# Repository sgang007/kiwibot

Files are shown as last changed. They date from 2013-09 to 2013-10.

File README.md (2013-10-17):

<p align="center">
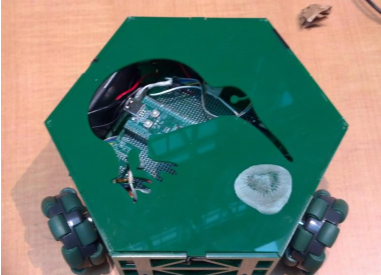
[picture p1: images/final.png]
  
</p>
# Introduction #

An omniwheel robot created for a class project. The robot uses three omniwheels mounted in a equilateral triangle formation to move in any direction without changing its orientation. A line following component was also added to be able to demo its movement easily. The CAD files for the body design, the circuit schematics, and the code are all included. Though only the simpler PID method was tested and used for the final project, I've also included another PID function written afterwards that would need to be tested to tweak the factors before use. 
All the code, cad files, and eagle files are included.

## Body Design ##

The frame was modeled in NX CAD. The part drawings were then saved as DXF files and printed out of .125”-thick, fluorescent green acrylic. The robot assembly was designed to be simple yet sturdy and was accomplished through a combination of press-fits, fastener screws, and hot glue.
The enclosed portion of the frame housed the three 6 volt battery packs, the cylindrical housing for the three motors, as well as the NU32’s PCB. The undercarriage held the motor gearboxes and attached omniwheels as well as the custom PCB with the H-bridges and phototransistor LED ring, described in detail below. The files are attached.

We used the faulhaber motor with encoder described here: http://www.robotroom.com/FaulhaberGearmotor.html 
Our main reason for using these was that they were available in the lab. But we had a few issues with it, such as being able to tighten the set screw. We did not have the right hex key available and so we just used a small screwdriver to tighten it whenever there was an issue. But by the end of the project, this had stripped the screw and made it impossible to tighten the wheels. Luckily we had already demoed by then, but it is the reason for not testing out the new PID.

## Circuit ##

<p align="center">
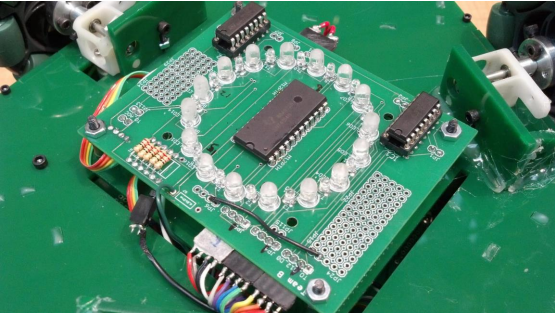
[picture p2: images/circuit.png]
  
</p>

We wanted line sensing, but it wasn't the main objective of the project so this part was kept simple and cheap. Just a ring of LEDs and phototransistors for the line detection. The ring of 16 LED/phototransistor pairs makes the detection cheap and orientation independent. 
We kept most of the circuit elements on the PCB on the underside of the robot where the LEDs would have to be. The phototransistors are connected to a MUX and cycled through by the PIC to read different points on the circle. The circuit was designed in EAGLE and the files are also included.
Images of the schematic are attached. Can't find the Eagle files right now...

## Code ##

The encoder counts are counted by polling the ports at a tiny interval (faster than that of the motor’s fastest rpm * encoder lines) and decoding the quadrature.

The sensing and movement:

(LED 7 was 90 degrees, straight ahead)

1.  If there is no previous forward point saved, set previous forward point to 7

2.  Cycle through LEDs and check “high” phototransistors (those over a dark color)

3.  Collect contiguous blocks of high LEDs (so if LEDs 1-4 were high, that would be one 
block)

4.  Compute the point distance between the previous forward point and the border points of 
each block.

5.  Update previous forward point to the point that is the shortest distance from the previous forward point. (thus 
distinguishing between the front and back of the path)

7.  Convert point to degree heading and pass to movement

The movement algorithm was a simple linear system that was solved for the velocities of each 
wheel. The three parameters were the x,y directions and the angular velocity which we set to 
0 in order to achieve movement without change in orientation. 
We solve for each wheel's velocity by using the amount it would contribute to each direction while keeping rotation zero

## PID ##

The simple PID method we used was to check the speed of the wheel that was supposed to spin the fastest (or pick one 
of the two if two were supposed to spin at equal speeds, like for straight ahead movement) and use it and proportions of it
as the target value to judge error of off for feedback.

Obviously it isn't perfect but it worked for the slower speeds 
with only very slight orientation changes after a while of demoing. But we had a more advanced method we hadn't fully tweaked 
by the time it was due and can't test now due to the broken screw. 

Once again use relative velocities, but make the target an angular velocity of 0.  The error would be amount off 0, and feedback affects all three wheels by k*relative velocity, so wheels are corrected differently 
based on how fast they are going, and wheels rotating the robot in the opposite direction are corrected by the opposite value. 

This looked like it could work better but it was a bit more complicated. And to get it really smooth and going at a decent speed, 
there is the issue of correcting current relative velocities to prevent the orientation change while also keeping target velocities in mind
so that velocities aren't corrected and kept at too low of a speed. And waiting too long after a heading change to correct would mean 
that the orientation would change too much between heading changes. Implementing that and ironing out such issues is the next step.

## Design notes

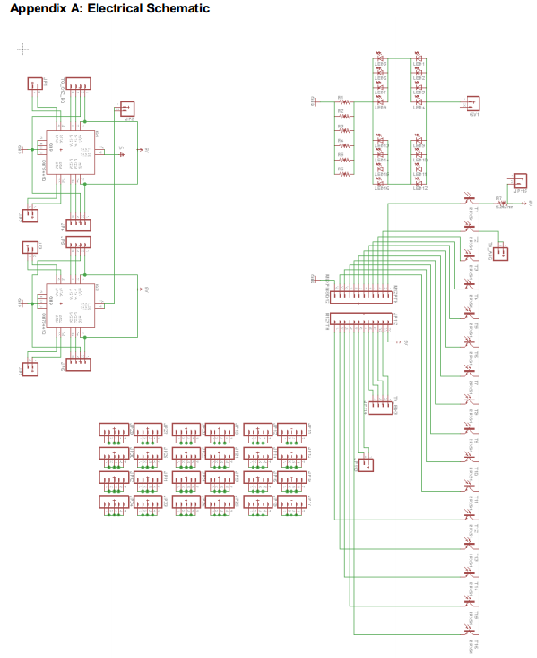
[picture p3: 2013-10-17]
images/circuitschematic.png

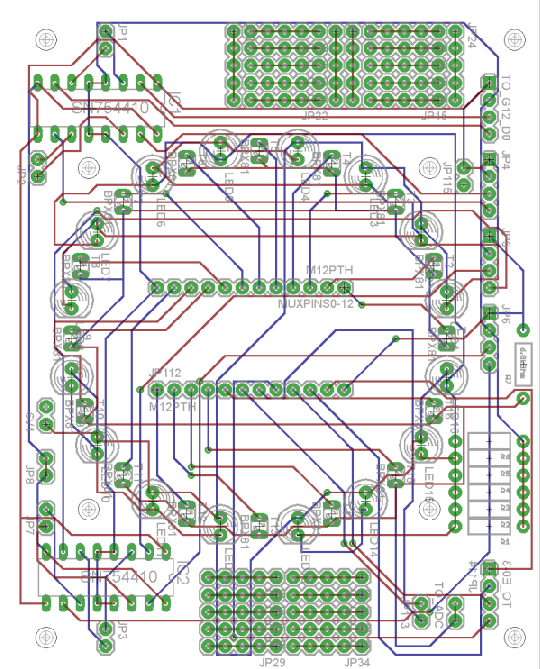
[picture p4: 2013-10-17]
images/pcb.png

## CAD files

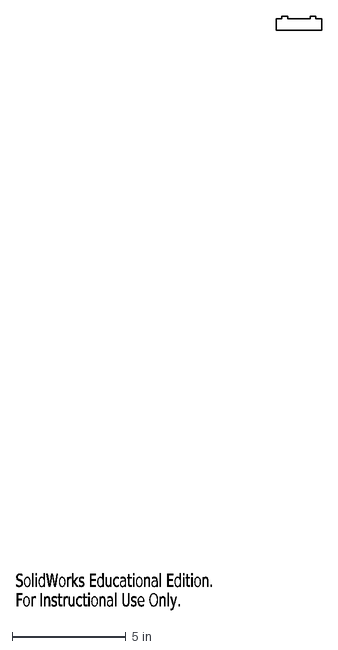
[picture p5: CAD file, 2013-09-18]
DXF/battsupp1.DXF
SolidWorks Educational Edition.
For Instructional Use Only.

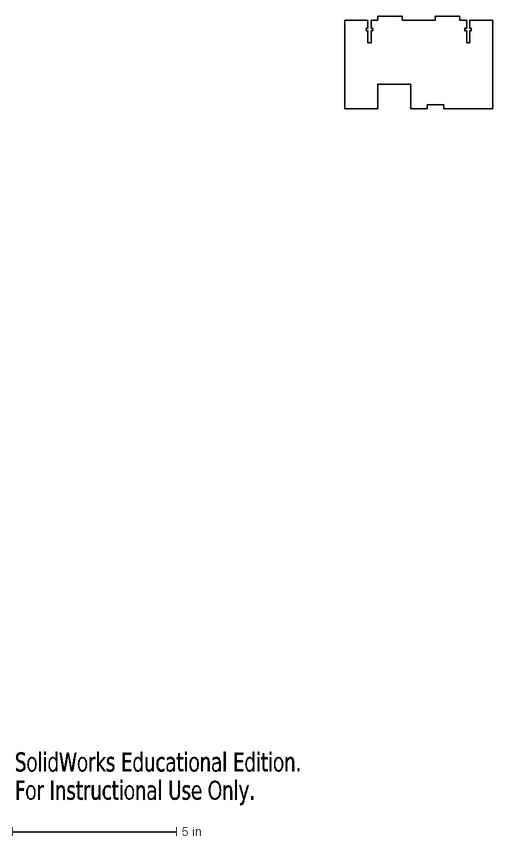
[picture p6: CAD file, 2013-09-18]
DXF/hexside mid.DXF
SolidWorks Educational Edition.
For Instructional Use Only.

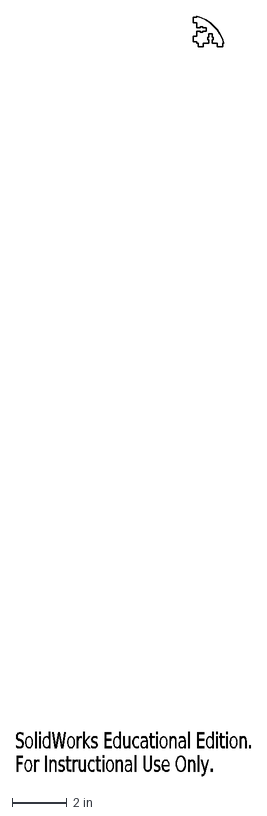
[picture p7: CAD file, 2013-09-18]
DXF/motorsupport2.DXF
SolidWorks Educational Edition.
For Instructional Use Only.

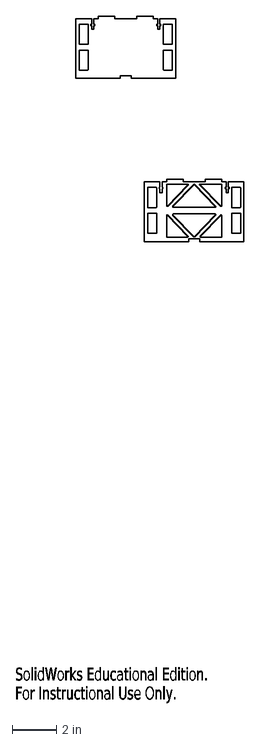
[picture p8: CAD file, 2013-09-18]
DXF/hexside none_0.DXF
SolidWorks Educational Edition.
For Instructional Use Only.

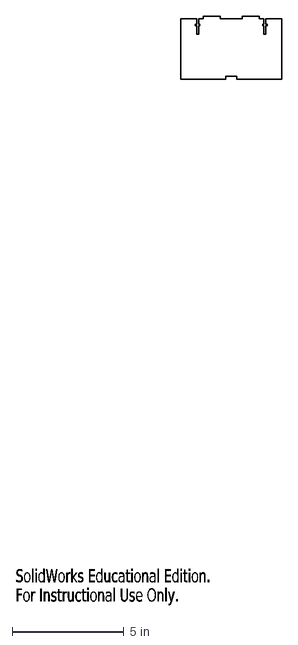
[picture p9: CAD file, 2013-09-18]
DXF/hexside none.DXF
SolidWorks Educational Edition.
For Instructional Use Only.

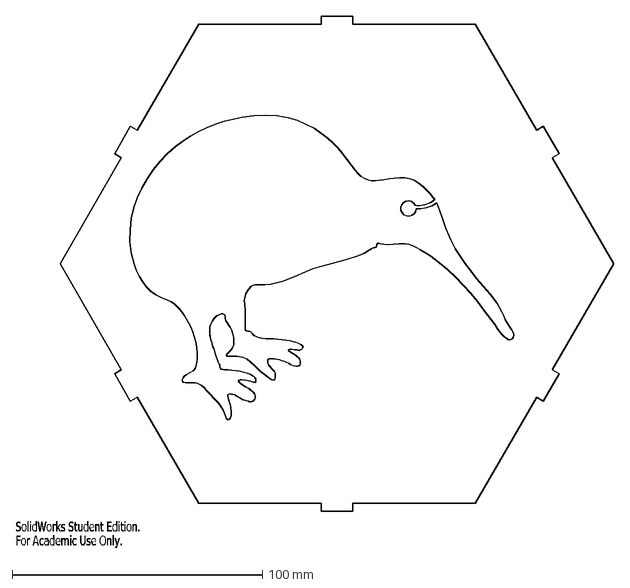
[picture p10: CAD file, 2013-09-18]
DXF/Part3.DXF
SolidWorks Student Edition.
For Academic Use Only.

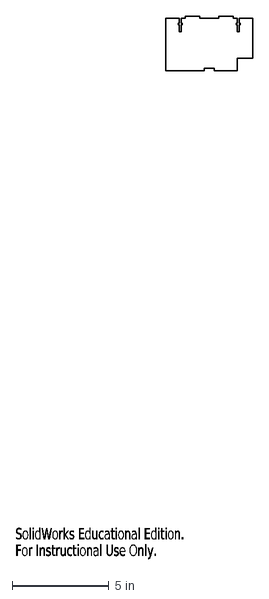
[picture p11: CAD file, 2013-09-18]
DXF/hexside.DXF
SolidWorks Educational Edition.
For Instructional Use Only.

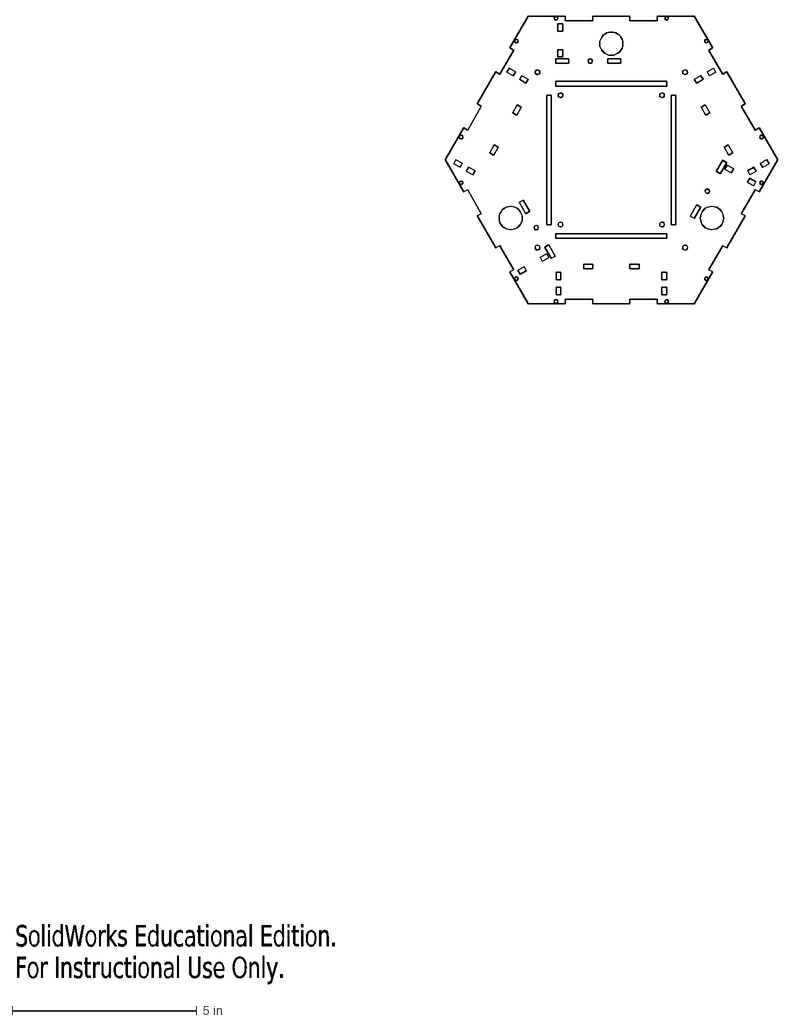
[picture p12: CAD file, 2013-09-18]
DXF/base.DXF
SolidWorks Educational Edition.
For Instructional Use Only.

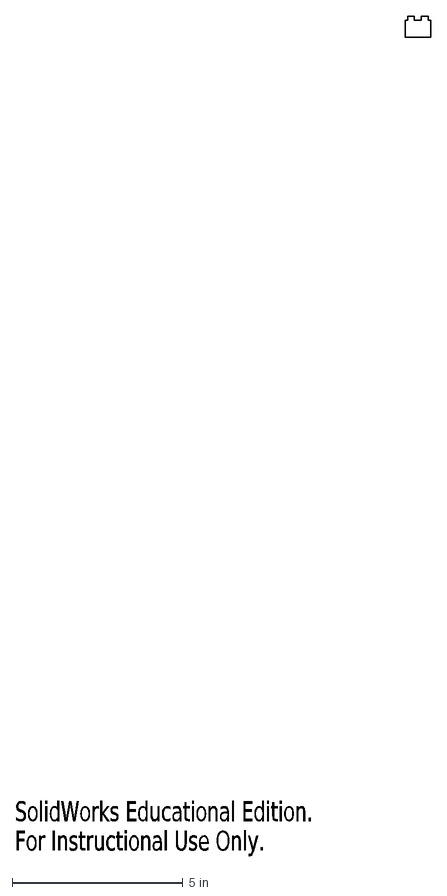
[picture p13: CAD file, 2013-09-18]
DXF/battsupp2.DXF
SolidWorks Educational Edition.
For Instructional Use Only.

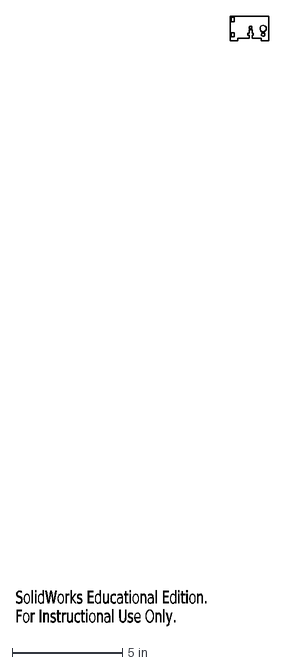
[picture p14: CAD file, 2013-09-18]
DXF/motor support1.DXF
SolidWorks Educational Edition.
For Instructional Use Only.

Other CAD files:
Parts/New Base.prt
Parts/assembly2.prt
Parts/battsupp1.prt
Parts/battsupp2.prt
Parts/boardsupport1.prt
Parts/motor support1.prt
Parts/motorsupport.prt
Parts/motorsupport2.prt

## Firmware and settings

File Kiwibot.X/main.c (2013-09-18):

#include "globals.h"
#include "sensing.h"
#include "movement.h"
//.5
//.01
//.005
void doStuff();
struct path_mark FP;
struct target T = {.prev_target_degs = 270,.target_degs = 270,.desired_components = {0,0,0}};
char dbg_message[100];
struct movement_data MS = {.speeds =
    {0, 0, 0}, .ref_speeds =
    {0, 0, 0}, .curr_state =
    {0, 0, 0}, .prev_state =
    {0, 0, 0}, .counts =
    {0, 0, 0}, .prev_10_counts =
    {0, 0, 0}, .prev_10_time =
    {0, 0, 0}, .curr_10_time =
    {0, 0, 0}, .motor_values =
    {0, 0, 0}, .motor_targets =
    {0, 0, 0}, .prev_motor_targets =
    {0, 0, 0}, .dir =
    {CTPS_TIMES_10, CTPS_TIMES_10, CTPS_TIMES_10}};
int encoder_states[2][2] = {
    {0, 3},
    {1, 2}
};
int curr_state;
int prev_state;
int temp_time;
const float upscaled_speed = .5;
float upscaled_vector = .5;
const float ref_speed = 30;
float ref_vec = 30;
const float kp = 0.01;
const float ki = 0.005;
const float kd;

void __ISR(_TIMER_1_VECTOR, IPL7AUTO)Timer1Handler(void) {
    MS.curr_state[0] = encoder_states[PORTEbits.RE0][PORTEbits.RE1];
    MS.curr_state[1] = encoder_states[PORTEbits.RE2][PORTEbits.RE3];
    MS.curr_state[2] = encoder_states[PORTEbits.RE5][PORTEbits.RE4];
    int i;
    for (i = 0; i < 3; i++) {
        if (MS.curr_state[i] > MS.prev_state[i]) {
            if (MS.dir[i] == -CTPS_TIMES_10) {
                //MS.counts[i] = 10 - (MS.counts[i] % 10);
                MS.dir[i] == CTPS_TIMES_10;
            }
            MS.counts[i]++;
        } else if (MS.curr_state[i] < MS.prev_state[i]) {
            if (MS.dir[i] == CTPS_TIMES_10) {
                //MS.counts[i] = 10 - MS.counts[i] % 10;
                MS.dir[i] == -CTPS_TIMES_10;
            }
            MS.counts[i]--;
        }
        MS.prev_state[i] = MS.curr_state[i];
        if ((MS.counts[i] % 10 == 0) && (MS.counts != MS.prev_10_counts)) {
            MS.prev_10_counts[i] = MS.counts[i];
            MS.curr_10_time[i] = ReadCoreTimer();
            if (MS.curr_10_time[i] < MS.prev_10_time[i]) {
                //TODO
            }
            //10 encoder counts, divided by change in core ticks,
            //times number of coreticks in a second (80 mil)
            //since 10 and 80 mil constant, change dir
            //MS.speeds[i] = MS.dir[i] / (MS.curr_10_time[i] - MS.prev_10_time[i]);
            MS.prev_10_time[i] = MS.curr_10_time[i];
        }
    }
    IFS0bits.T1IF = 0;
}

void main(void) {
    NU32_Startup();
    //read sensors
    //get angle of movement from sensor marks
    //keep up encoder counts, velocity vectors of the three motors
    //incorporate velocity information and use angle heading to set motor vectors
    // cache on, min flash wait, interrupts on, LED/button init, UART init
    T1CON = 0x0; // Stop timer and clear control register,
    // prescaler at 1:1,internal clock source
    TMR1 = 0x0; // Clear timer register
    PR1 = 100000; // Load period register
    IPC1bits.T1IP = 7;
    IPC1bits.T1IS = 3;
    IFS0bits.T1IF = 0;
    IEC0bits.T1IE = 1;
    T1CONSET = 0x8000; // Start timer
    //NU32_WriteUART1("Initialized\n");
    initMovement();
    //NU32_WriteUART1("Movement initialized\n");
    initSensing();
    //NU32_WriteUART1("Sensing initialized\n");
    int motor_choice, dir;
    float spd;
    stop();
    doStuff();
}

void doStuff() {
    float ratios[3] = {0, 0, 0};
    float max_wheel_speed = 0;
    float err[3] = {0, 0, 0};
    float prev_err[3] = {0, 0, 0};
    int i;
    int change = 0;
    int max = 0;

    while (1) {
        initAngles();
        getFrontPath(&FP);
        if(FP.len==-1){
            NU32_WriteUART1("lost\n");
            if(T.prev_target_degs < 180){
                T.target_degs = T.prev_target_degs + 180;
            }else{
                T.target_degs = T.prev_target_degs - 180;
            }
            
        }else{
            T.prev_target_degs = T.target_degs;
            getAngleOfPath(&FP,&T);
        }

        sprintf(dbg_message,"target degrees: %f\n",T.target_degs);
        NU32_WriteUART1(dbg_message);
        T.target_rads = deg2Rads(T.target_degs);

        calcVectors(&T, &MS);
        change = 0;
        for (i = 0; i < 3; i++) {
            if (MS.prev_motor_targets[i] != MS.motor_targets[i]) {
                change = 1;
                break;
            }
        }
        for (i = 0; i < 3; i++) {
            MS.prev_motor_targets[i] = MS.motor_targets[i];
        }
        //only have to recalculate ratios and shit if motor targets are different
        if (change) {
            for (i = 0; i < 3; i++) {
                if (fabs(MS.motor_targets[i]) > fabs(MS.motor_targets[max])) {
                    max = i;
                }
            }

            max_wheel_speed = MS.motor_targets[max];
            if (max_wheel_speed < 0) {
                upscaled_vector = -upscaled_speed;
            } else {
                upscaled_vector = upscaled_speed;
            }
            ratios[max] = 1;
            for (i = 0; i < 3; i++) {
                if (i != max) ratios[i] = MS.motor_targets[i] / max_wheel_speed;
                MS.motor_values[i] = ratios[i] * upscaled_vector;
            }

            for (i = 0; i < 3; i++) {
                setMotor(i, MS.motor_values[i]);
            }
        }
        measureSpeeds(&MS);
        for (i = 0; i < 3; i++) {
            //goals are set to a ratio of the fastest
            if (i != max) {
                MS.ref_speeds[i] = MS.speeds[max] * ratios[i];
                err[i] = MS.ref_speeds[i] - MS.speeds[i];
                //previous motor value gets a bump if not fast enough, or slowed if it is
                //next iteration uses this value, if the new speed was good enough, then it is maintained since the err term will be zero
                MS.motor_values[i] = MS.motor_values[i] + err[i] * kp + (err[i] - prev_err[i]) * ki;
                prev_err[i] = err[i];
            }
            setMotor(i, MS.motor_values[i]);
        }
    }

}

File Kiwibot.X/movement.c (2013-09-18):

#include "movement.h"
//get angle and power motors in a way that it moves at that angle
char move_msg[100];

//Variables used throughout movement functions
float angles[SENSOR_COUNT];
float rads[SENSOR_COUNT];
int const MEASURE_TIME = 200000;
//constant matrix assigned at runtime used to calculate desired components
float movement_matrix[3][3];
//angle of the three motors, constants chosen dependant on reference point
float motor_angles[3];
//desired vx, vy, rw

void moveAt(struct target* t,struct movement_data *ms) {
    //desired x speed, yspeed, rotation

    calcVectors(t,ms);
        sprintf(move_msg, "desired components %f %f %f \n", t->desired_components[0],
                t->desired_components[1], t->desired_components[2]);

    NU32_WriteUART1(move_msg);
      sprintf(move_msg, "motor values %f %f %f\n", ms->motor_values[0],
                ms->motor_values[1], ms->motor_values[2]);
    NU32_WriteUART1(move_msg);
    

    //get mark or angle? decide between getting angle from mark here or in sensing
    //then use velocity information from encoders to figure what the motors need
    //to be set to to move at that angle
}
void initAngles(){
    int i;
    for (i = 0; i < SENSOR_COUNT; i++) {
        angles[i] = 236.25 - 22.5 * i;
        if (angles[i] < 0) {
            angles[i] += 360;
        }
}
}
void initMovement() {
    //set up angles
    int i;
    float circ = 2 * 6.28318530718;
    for (i = 0; i < SENSOR_COUNT; i++) {
        angles[i] = 236.25 - 22.5 * i;
        if (angles[i] < 0) {
            angles[i] += 360;
        }
        rads[i] = deg2Rads(angles[i]);
        sprintf(move_msg, "angle at sensor %d is %f\n",i,angles[i]);
        NU32_WriteUART1(move_msg);
        rads[i] = ((float) circ) / ((float) SENSOR_COUNT) * i;
    }
    motor_angles[0] = deg2Rads(90);
    motor_angles[1] = deg2Rads(330);
    motor_angles[2] = deg2Rads(210);
    initMotors();

}

void setMotor(int motor_num, float speed) {
    switch (motor_num) {
        case 0:
            if (speed < 0) {
                LATGbits.LATG12 = 0;
                OC1RS = 1999 * -1 * speed;
            }else{
                LATGbits.LATG12 = 1;
                OC1RS = 1999 - 1999 * speed;
            }
            break;
        case 1:
            if (speed < 0) {
                LATGbits.LATG13 = 0;
                OC2RS = 1999 * -1* speed;
            }else{
                LATGbits.LATG13 = 1;
                OC2RS = 1999 - 1999 * speed;
            }
            break;
        case 2:
            if (speed < 0) {
                LATGbits.LATG14 = 0;
                OC3RS = 1999 * -1 * speed;
            }else{
                LATGbits.LATG14 = 1;
                OC3RS = 1999 - 1999 * speed;
            }
            break;


    }
}

void setMotor1(float speed, int dir) {
    if (dir == 0) {
        LATGbits.LATG12 = 0;
        OC1RS = 1999 * speed;
    }
    if (dir == 1) {
        LATGbits.LATG12 = 1;
        OC1RS = 1999 - 1999 * speed;
    }
}

void setMotor2(float speed, int dir) {
    if (dir == 0) {
        LATGbits.LATG13 = 0;
        OC2RS = 1999 * speed;
    }

    if (dir == 1) {
        LATGbits.LATG13 = 1;
        OC2RS = 1999 - 1999 * speed;
    }
}

void setMotor3(float speed, int dir) {
    if (dir == 0) {
        LATGbits.LATG14 = 0;
        OC3RS = 1999 * speed;
    }

    if (dir == 1) {
        LATGbits.LATG14 = 1;
        OC3RS = 1999 - 1999 * speed;
    }
}

void initMotors() {
    // DIR for motors 1 - 3
    TRISGbits.TRISG12 = 0;
    TRISGbits.TRISG13 = 0;
    TRISGbits.TRISG14 = 0;

    //encoder lines A,B for motors 1-2
    TRISEbits.TRISE0 = 1;
    TRISEbits.TRISE1 = 1;
    TRISEbits.TRISE2 = 1;
    TRISEbits.TRISE3 = 1;
    TRISEbits.TRISE4 = 1;
    TRISEbits.TRISE5 = 1;

    // use TIMER2 for the PWM
    T2CONbits.TCKPS = 2; // Timer2 prescaler N=4 (1:4)
    PR2 = 1999; // period = (PR2+1) * N * 12.5 ns = 100 us, 10 kHz
    TMR2 = 0; // initial TMR2 count is 0

    // use OC5 (on D4)
    OC1CONbits.OCM = 0b110; // PWM mode without fault pin; other OC1CON bits are defaults
    OC1RS = 500; // duty cycle = OC1RS/(PR2+1) = 25%
    OC1R = 500; // initialize before turning OC1 on; then it is read-only

    OC2CONbits.OCM = 0b110; // PWM mode without fault pin; other OC1CON bits are defaults
    OC2RS = 500; // duty cycle = OC1RS/(PR2+1) = 25%
    OC2R = 500; // initialize before turning OC1 on; then it is read-only

    OC3CONbits.OCM = 0b110; // PWM mode without fault pin; other OC1CON bits are defaults
    OC3RS = 500; // duty cycle = OC1RS/(PR2+1) = 25%
    OC3R = 500; // initialize before turning OC1 on; then it is read-only

    // turn them on
    T2CONbits.ON = 1; // turn on Timer2
    OC1CONbits.ON = 1; // turn on OC1
    OC2CONbits.ON = 1; // turn on OC2
    OC3CONbits.ON = 1; // turn on OC3

    // initially off
    OC1RS = 0;
    OC2RS = 0;
    OC3RS = 0;
    LATGbits.LATG12 = 1;
    LATGbits.LATG13 = 1;
    LATGbits.LATG14 = 1;
}

void calcVectors(struct target* t, struct movement_data* ms) {
    int i;
    int j;
    t->desired_components[0] = cosf(t->target_rads);
    t->desired_components[1] = sinf(t->target_rads);
    t->desired_components[2] = 0;
    ms->motor_targets[0] = -.666666f * t->desired_components[0];
    ms->motor_targets[1] = .33333f * t->desired_components[0] + .57735f * t->desired_components[1];
    ms->motor_targets[2] = -.33333f * t->desired_components[0]+ .57735f * t->desired_components[1];
}

void setMotors(struct movement_data* ms) {
    setMotor(0,ms->motor_values[0]);
    setMotor(1,ms->motor_values[1]);
    setMotor(2,ms->motor_values[2]);
}

float deg2Rads(float angle) {
    return angle * 3.14159 / 180;
}

void getAngleOfPath(struct path_mark* f, struct target* t) {
    int s = f->start;
    int e = f->end;
    t->target_degs = (angles[s] + angles[e]) / 2;
    sprintf(move_msg, "from %d to %d with %f %f is an angle of %f\n",f->start,f->end,angles[s],angles[e],t->target_degs);
    NU32_WriteUART1(move_msg);
}
//map each speed value to a duty cycle
//but, the the wheel with the highest speed in a given command uses this set value
//the other two are only set to this initially, then are adjusted with pid
//to maintain the speed ratio to the fastest wheel
void measureSpeeds(struct movement_data* ms) {
    int i = 0;
    int count_diff[3];
    for(i = 0;i < 3;i++){
        count_diff[i] = ms->counts[i];
    }
    waitFor(MEASURE_TIME);
    //since we are measuring the same for all, and we only need relative speeds,
    //do we need to do any dividing for speed?
    for(i = 0;i < 3;i++){
        count_diff[i] = ms->counts[i] - count_diff[i];
        ms->speeds[i] = count_diff[i];
    }
    
}
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
